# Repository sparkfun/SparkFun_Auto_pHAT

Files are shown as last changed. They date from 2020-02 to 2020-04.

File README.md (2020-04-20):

SparkFun Auto pHAT for Raspberry Pi (Qwiic)
========================================

SparkFun Auto pHAT for Raspberry Pi (Qwiic)) (https://www.sparkfun.com/products/16328)

[*SparkFun Auto pHAT for Raspberry Pi (Qwiic) (ROB-16328)*](https://www.sparkfun.com/products/16328)

The SparkFun Auto pHAT for Raspberry Pi is an all in one robotics package that focuses on quickly adding robot functionality and support to your Raspberry Pi or other single-board computer. The Auto pHAT can drive two small DC motors with or without encoders and up to four servo motors in a straightforward manner via an I<sup>2</sup>C connection. The servo control is based on the [SparkFun servo pHAT](https://www.sparkfun.com/products/15316) and thanks to its I<sup>2</sup>C capabilities, this PWM add-on saves the Raspberry Pi's GPIO pins, allowing you to use them for other purposes. We have also provided a Qwiic connector for easy interfacing with the I<sup>2</sup>C bus using the [Qwiic system](https://www.sparkfun.com/qwiic). Whether you use the Auto pHAT with a Raspberry Pi, NVIDIA, Jetson Nano, Google Coral, or other SBC, it makes for a unique robotics addition for and board with a 2x20 GPIO.

The DC motor control comes from the same 4245 PSOC and 2-channel motor ports system used on the [SparkFun Qwiic Motor Driver](https://www.sparkfun.com/products/15451). This provides 1.2A steady state drive per channel (1.5A peak) and 127 levels of DC drive strength. The SparkFun Auto pHAT also supports up to two motor encoders thanks to the onboard ATTINY84A to provide more precise movement to your creation! 

Additionally, the Auto pHAT has an on-board ICM-20948 9DOF IMU for all your motion sensing needs. This enables your robot to access the 3-Axis Gyroscope with four selectable ranges, 3-Axis Accelerometer, again with four selectable ranges, and 3-axis magnetometer with an FSR of ±4900µT.

Power to the SparkFun Auto pHAT can be supplied through USB-C connector or external power. This will power either the motors only, or power the motors as well as the Raspberry Pi that is connected to the HAT. This USB-C connector can also be used to hook up the Pi via serial port connection to avoid having to use a monitor and keyboard for setting up the Pi. We've even added power protection circuits to the design, to avoid damage to power sources.

For reference on programming the ATTINY84:

FUSE BITS:
(Set fuses to run at 8MHz internal)
(Disable Brown Out Detect)

* LowFuse 0xE2 
* HighFuse 0xDF
* ExtendedFuse 0xFF

Repository Contents
-------------------

* **/Documentation** - Data sheets, additional product information
* **/Hardware** - Eagle design files (.brd, .sch)
* **/Hardware/Production** - Production panel files and gerbers (.brd)
* **/Firmware** - Firmware for the Dual Encoder Reader IC (ATTiny84) and the Motor Driver IC (4245 PSOC)

Documentation
--------------

* **[Hookup Guide](https://learn.sparkfun.com/tutorials/sparkfun-auto-phat-hookup-guide)** - Basic hookup guide for the SparkFun Auto pHAT for Raspberry Pi (Qwiic).

License Information
-------------------

This product is _**open source**_! 

Please review the LICENSE.md file for license information. 

If you have any questions or concerns on licensing, please contact technical support on our [SparkFun forums](https://forum.sparkfun.com/viewforum.php?f=152).

Distributed as-is; no warranty is given.

- Your friends at SparkFun.

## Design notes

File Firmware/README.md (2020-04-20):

SparkFun Auto pHAT for Raspberry Pi (Qwiic)
========================================

The SparkFun Auto pHAT for Raspberry Pi Has two separate pieces of firmware:

(1) The Motor Controller firmware on the 4245 PSOC on the Auto pHAT is identical to the firmware found on the [SparkFun Qwiic Motor Driver](https://www.sparkfun.com/products/15451).

[Serial Controller Motor Driver Firmware](https://github.com/sparkfun/Serial_Controlled_Motor_Driver)

(2) The Encoder Reader firmware on the ATTiny84 can be found at the following Github Repository:

[Qwiic Dual Encoder Reader Firmware](https://github.com/sparkfun/Qwiic_Dual_Encoder_Reader)

For reference on programming the ATTINY84:

FUSE BITS:
(Set fuses to run at 8MHz internal)
(Disable Brown Out Detect)

* LowFuse 0xE2 
* HighFuse 0xDF
* ExtendedFuse 0xFF

License Information
-------------------

This product is _**open source**_! 

Please review the LICENSE.md file for license information. 

If you have any questions or concerns on licensing, please contact technical support on our [SparkFun forums](https://forum.sparkfun.com/viewforum.php?f=152).

Distributed as-is; no warranty is given.

- Your friends at SparkFun.

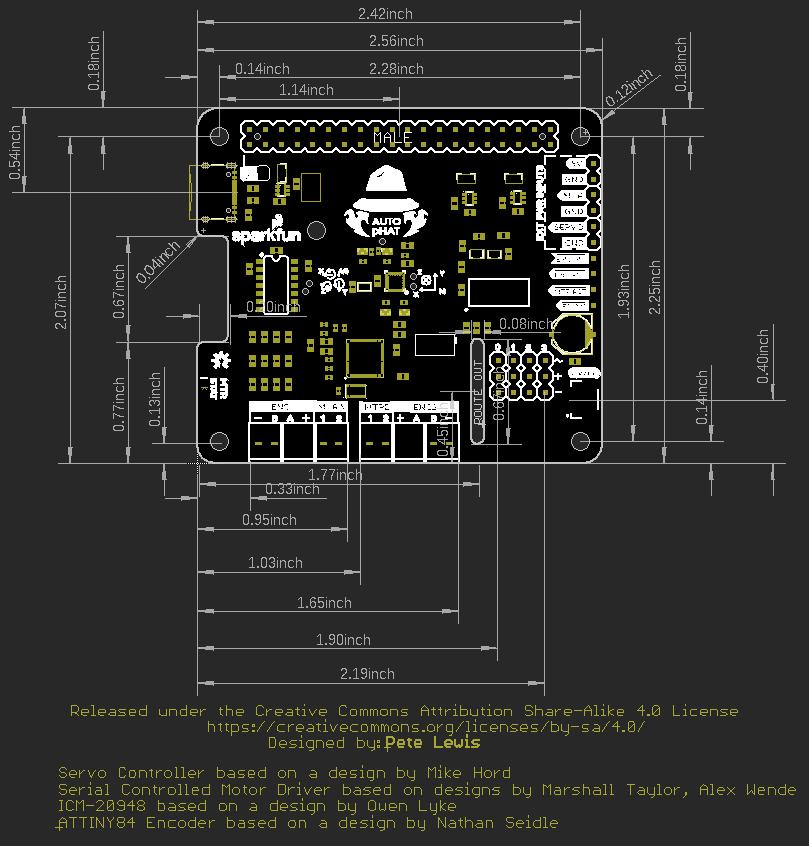
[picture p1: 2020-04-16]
Hardware/SparkFun_Auto_pHAT_Dimensions.png

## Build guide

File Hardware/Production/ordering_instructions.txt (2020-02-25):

panel size, 221x122mm
PCB thickness, 1.6mm
number of layers, 2
soldermask color, Red
silkscreen color, White
oz copper, 1oz
finish, HASL lead free
stencils, top+bottom
pcs per panel, 6
min trace width, 0.1778mm / 0.0070in
min drill size, 0.3500mm / 0.0138in

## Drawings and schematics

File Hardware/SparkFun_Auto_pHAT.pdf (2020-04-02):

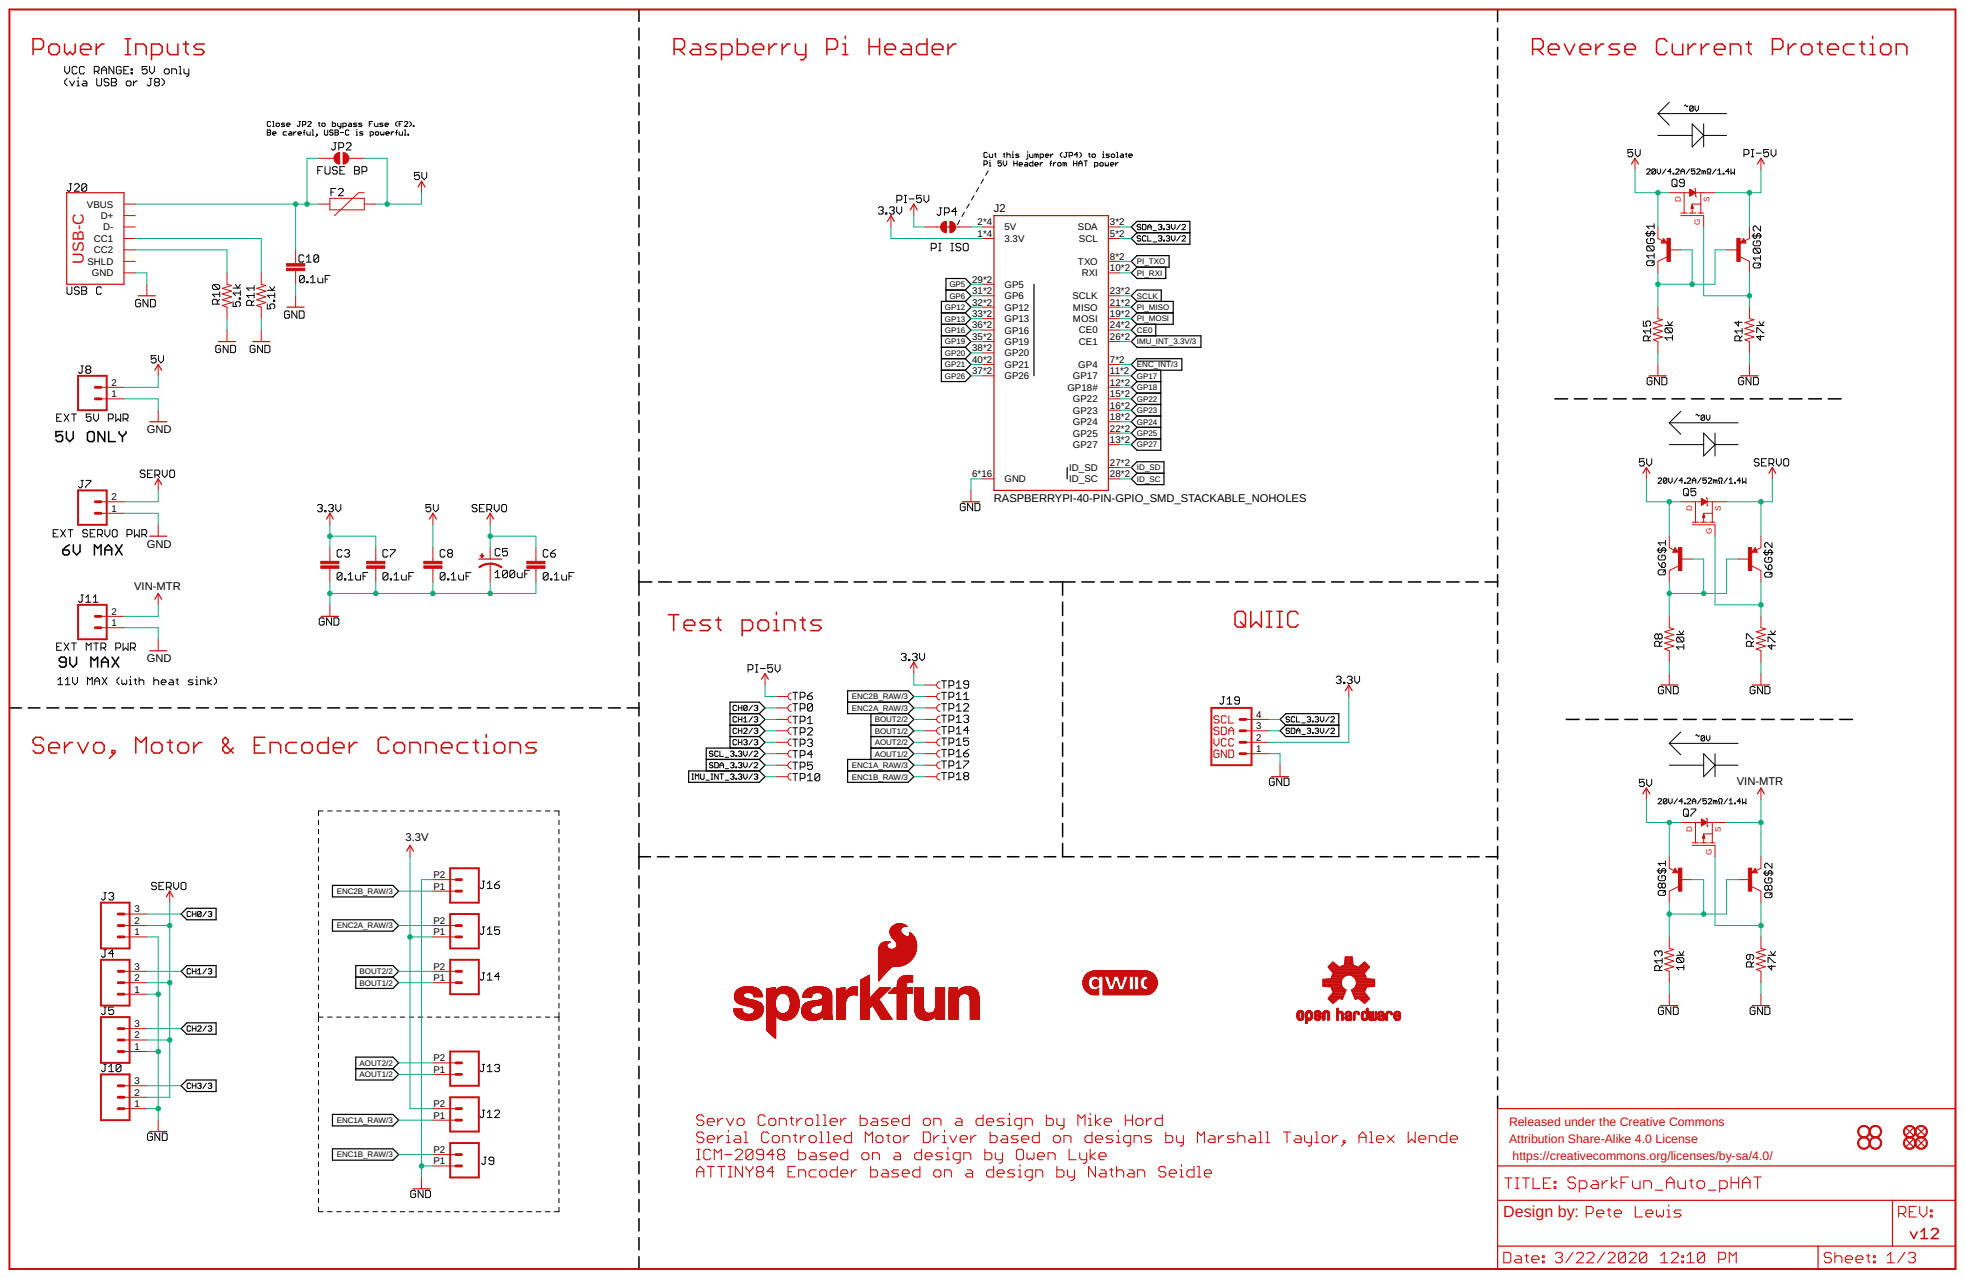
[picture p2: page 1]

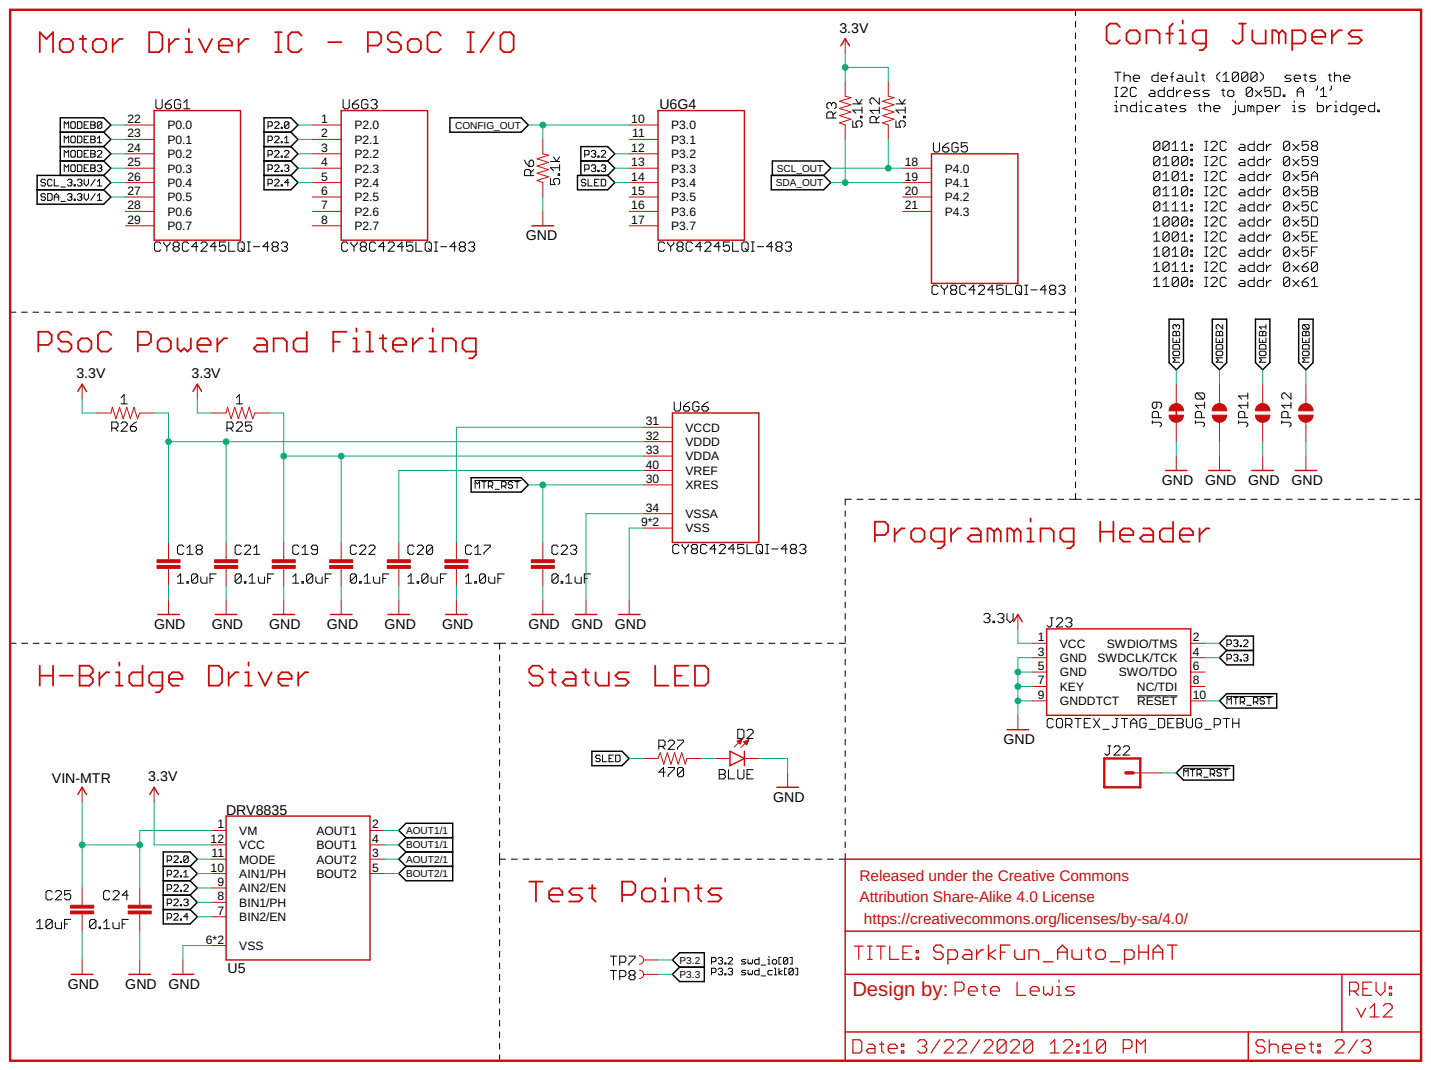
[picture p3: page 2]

GND GND

Released under the Creative Commons Attribution Share-Alike 4.0 License

https://creativecommons.org/licenses/by-sa/4.0/

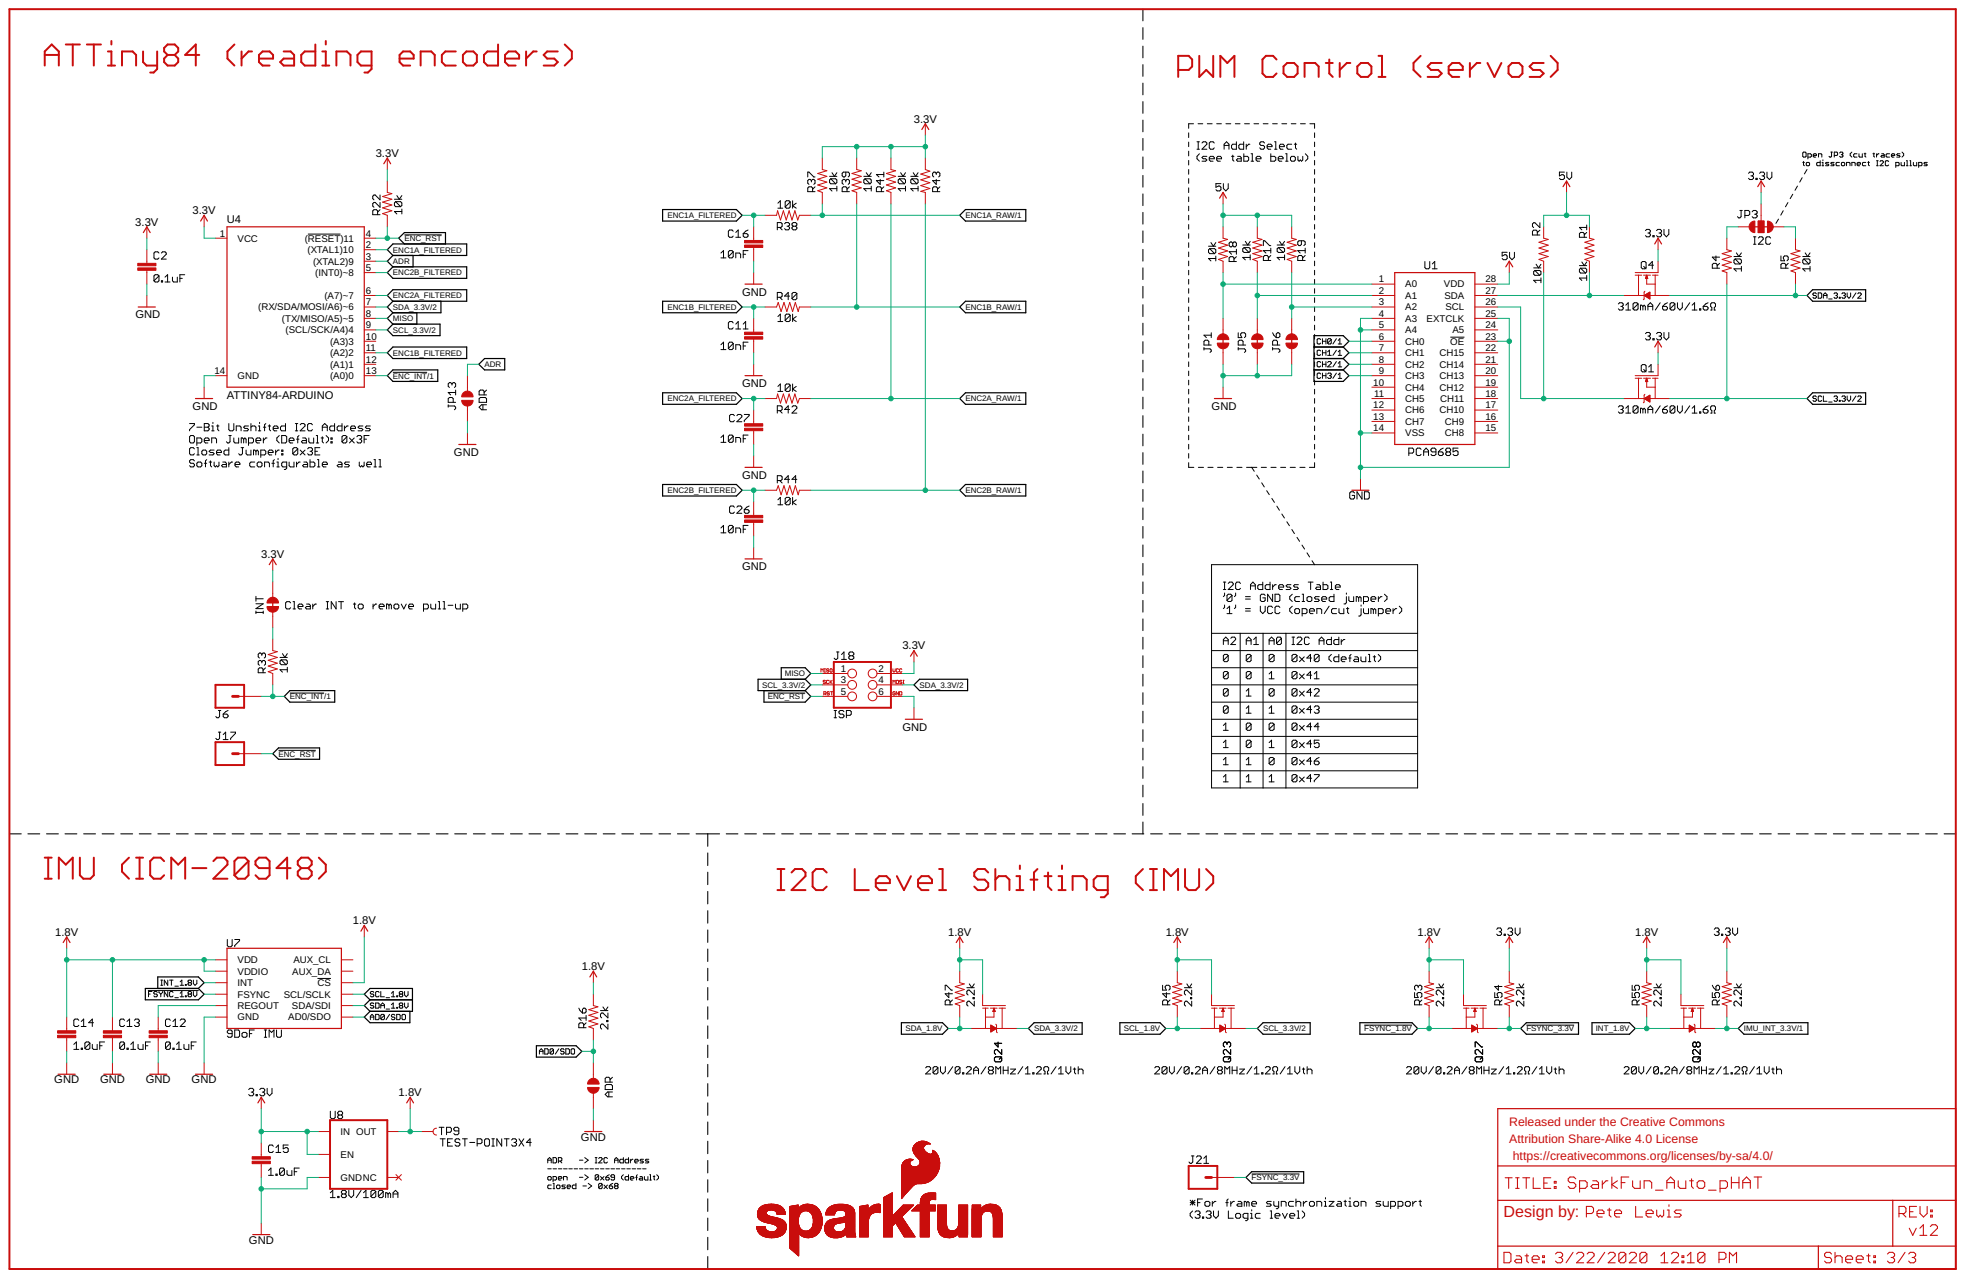
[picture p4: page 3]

SDA/SDI VDD
VDDIO
INT REGOUT SCL/SCLK
FSYNC GND

Released under the Creative Commons Attribution Share-Alike 4.0 License

https://creativecommons.org/licenses/by-sa/4.0/ Design by:

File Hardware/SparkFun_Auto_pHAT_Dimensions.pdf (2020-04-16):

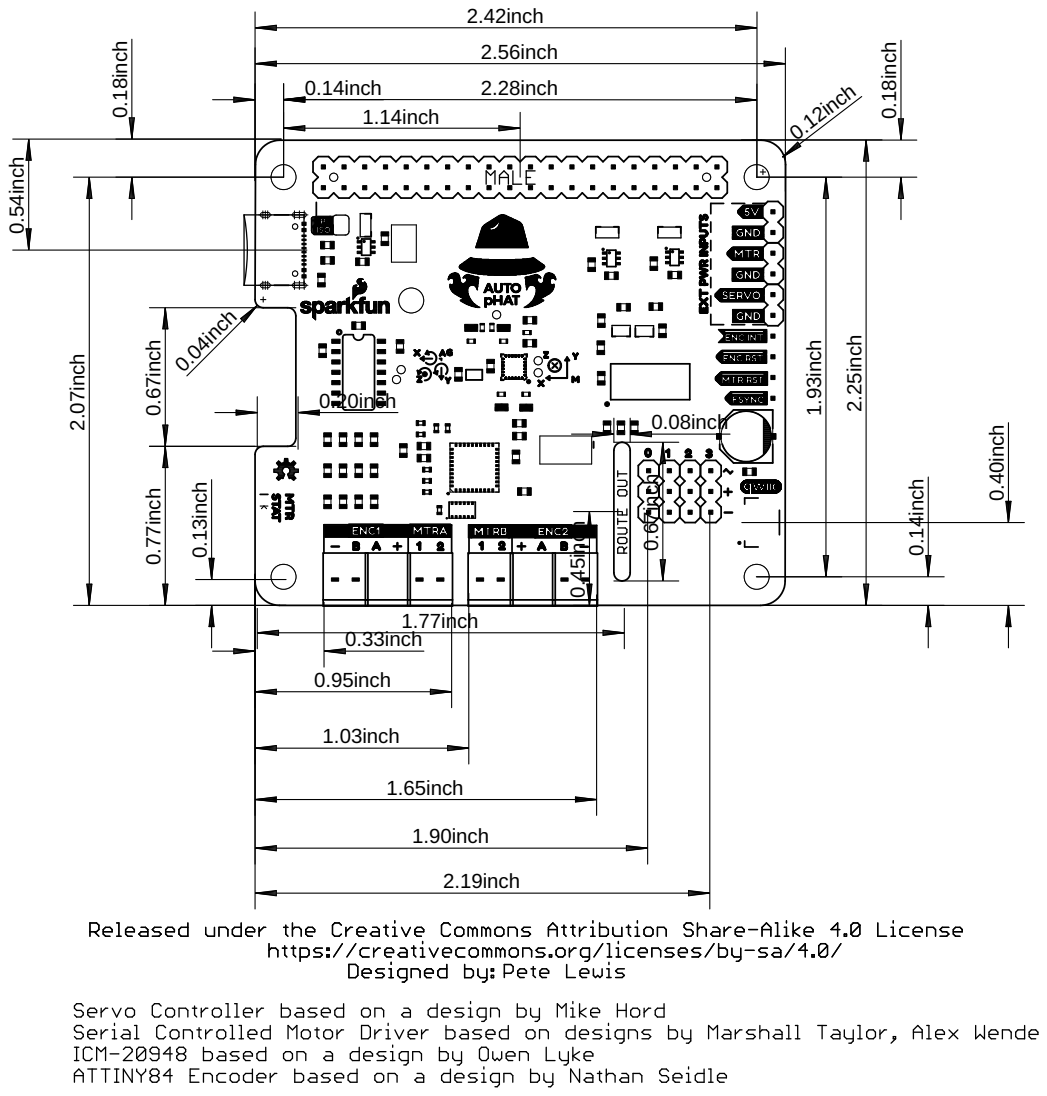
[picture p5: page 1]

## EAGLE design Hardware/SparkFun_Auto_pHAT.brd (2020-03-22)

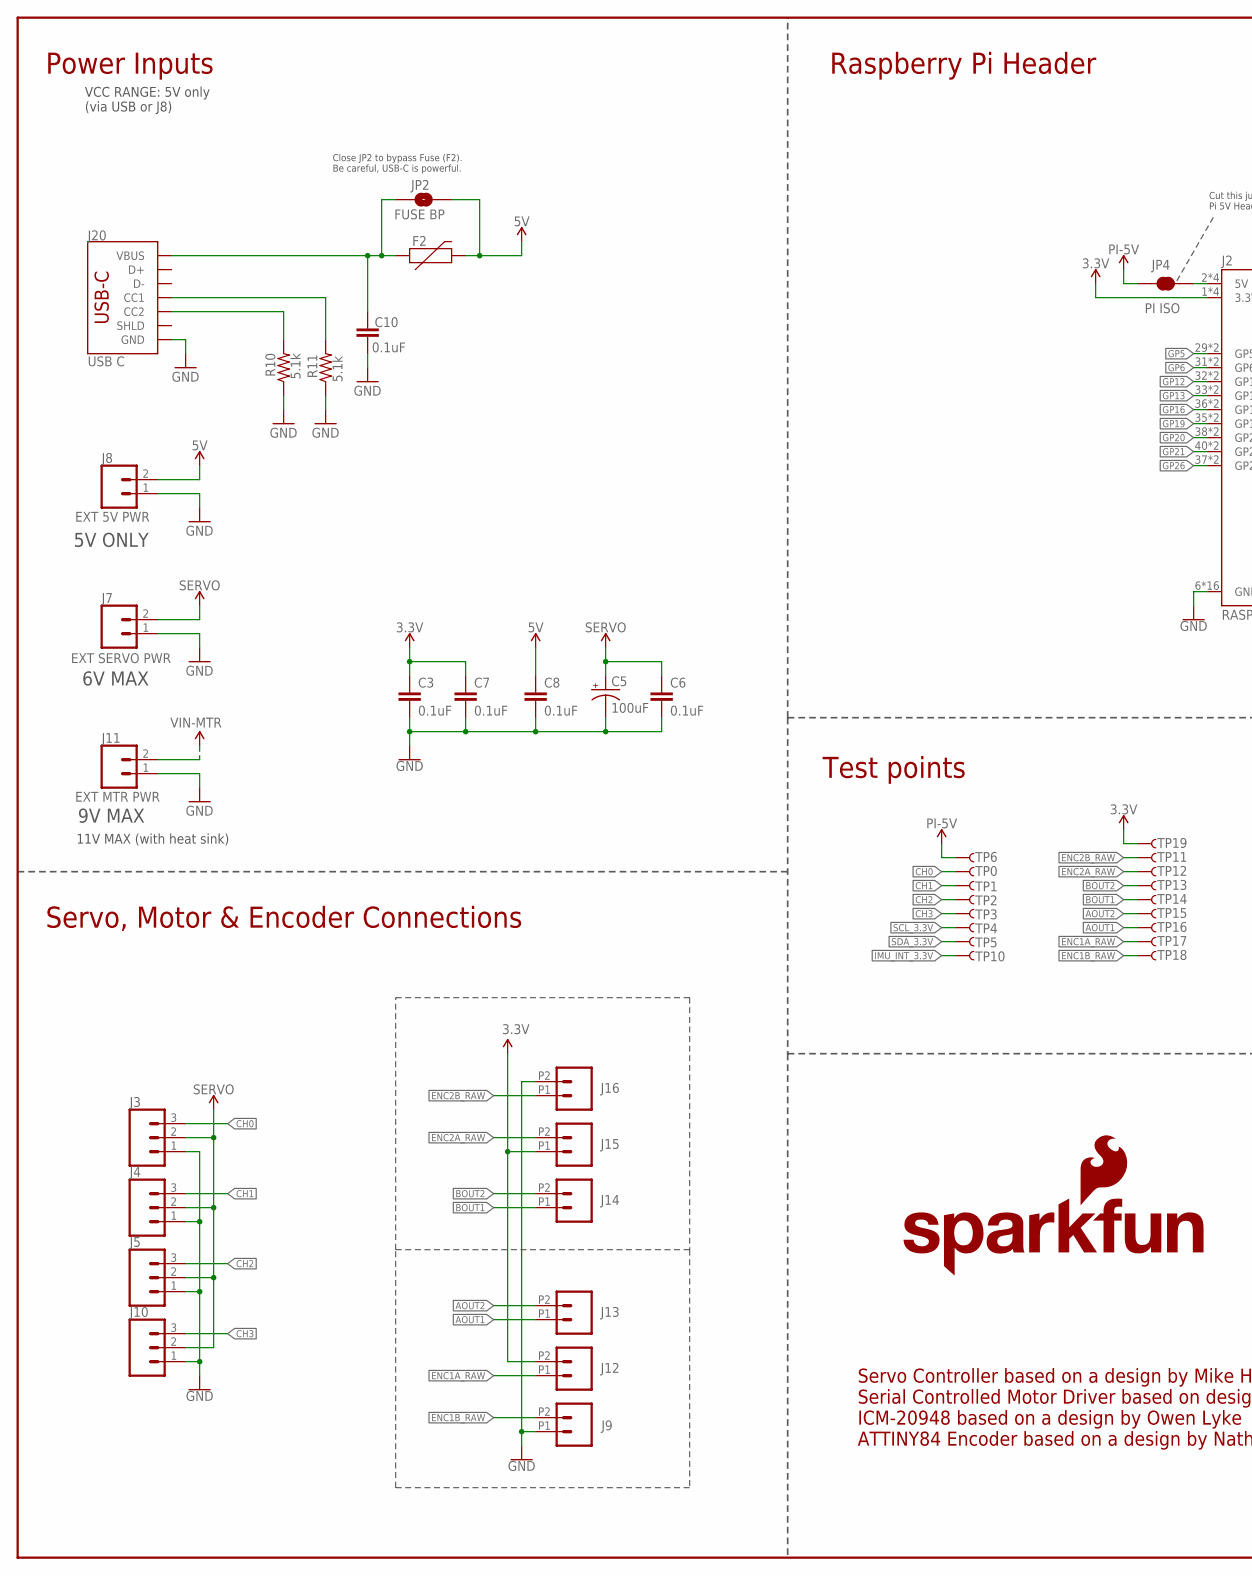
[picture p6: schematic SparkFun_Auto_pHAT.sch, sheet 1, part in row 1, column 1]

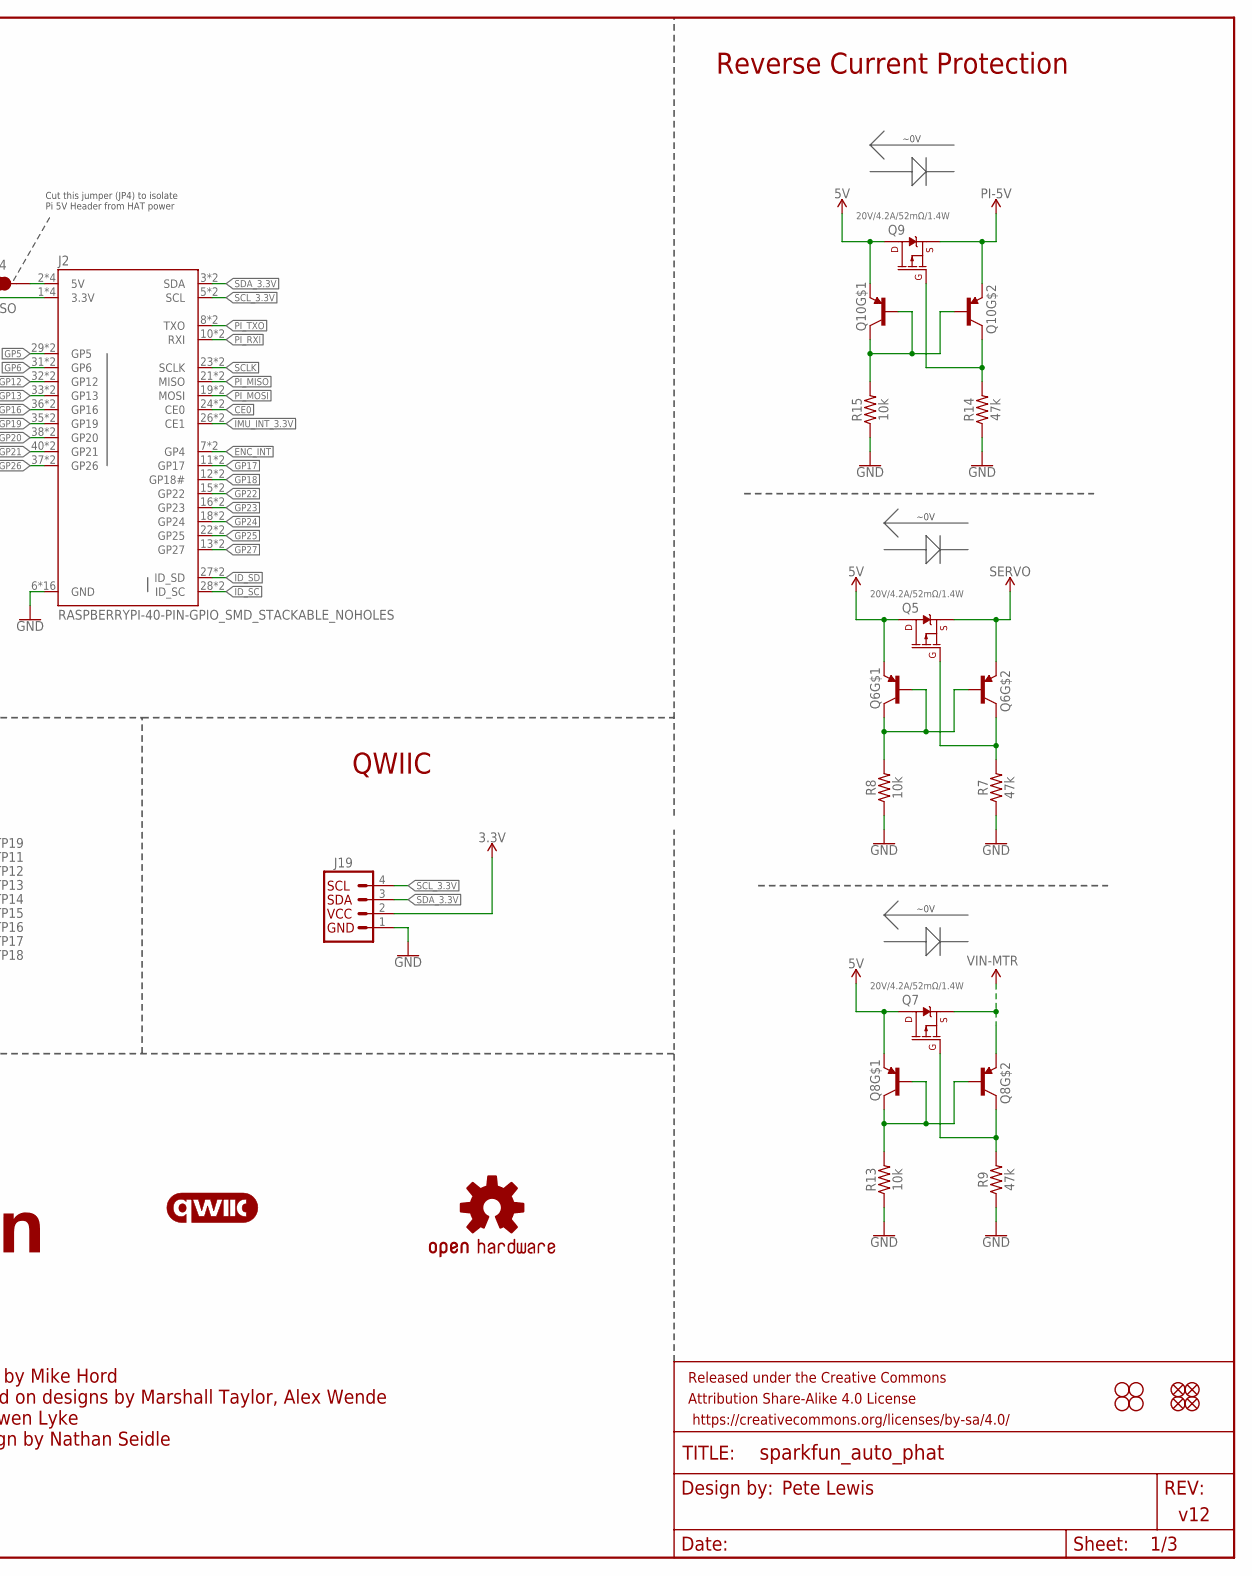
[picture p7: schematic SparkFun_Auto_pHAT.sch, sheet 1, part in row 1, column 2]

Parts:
C3, C6, C7, C8, C10: 0.1uF; 0603
C5: 100uF; PANASONIC_D
F2: 16V/2.5A(5A TRIP); 1812
FD5, FD6, FD7, FD8: FIDUCIALUFIDUCIAL; FIDUCIAL-MICRO
FRAME2: FRAME-LEDGER; CREATIVE_COMMONS
H9, H10, H11, H12: STAND-OFFTIGHT; STAND-OFF-TIGHT
J2: RASPBERRYPI-40-PIN-GPIO_SMD_STACKABLE_NOHOLES; RASPBERRY_PI_HAT_40_PIN_SMD_STACKABLE_NOHOLES
J3, J4, J5, J10: CONN_03LOCK; 1X03_LOCK
J7: EXT SERVO PWR; 1X02
J8: EXT 5V PWR; 1X02
J9, J13, J14, J16: CONN_02LG_DRILL; 1X02_2.54_SCREWTERM_LG_DRILL
J11: EXT MTR PWR; 1X02
J12, J15: CONN_022.54MM_SCREWTERM; 1X02_2.54_SCREWTERM
J19: QWIIC_CONNECTORJS-1MM; JST04_1MM_RA
J20: USB C; USB-C-16P
JP2: FUSE BP; SMT-JUMPER_2_NO_SILK
JP4: PI ISO; SMT-JUMPER_2_NC_TRACE_SILK
LOGO1: SFE_LOGO_NAME_FLAME.1_INCH; SFE_LOGO_NAME_FLAME_.1
LOGO2: OSHW-LOGOS; OSHW-LOGO-S
Q5, Q7, Q9: 20V/4.2A/52mΩ/1.4W; SOT23-3
Q6, Q8, Q10: TRANS_PNP_DUALSOT-363; SOT363_PHILIPS
R7, R9, R14: 47k; 0603@1
R8, R13, R15: 10k; 0603@1
R10, R11: 5.1k; 0603@1
TP0, TP1, TP2, TP3, TP6, TP10, TP11, TP12, TP13, TP14, TP15, TP16, TP17, TP18: TEST-POINT3X4; PAD.03X.04
TP4, TP5, TP19: TEST-POINTTP_15TH_THRU; TP_15TH
U$1: QWIIC_LOGO_5MM; QWIIC_5MM

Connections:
3.3V: C3.1, C7.1, J2.1 (3.3V), J2.1B (3.3V), J2.17 (3.3V), J2.17B (3.3V), J12.P2 (2), J15.P1 (1), J19.2, TP19.P$1; also elsewhere on the board
5V: C8.1, F2.2, J8.2, JP2.2, Q5.3 (D), Q6.1 (E), Q7.3 (D), Q8.1 (E), Q9.3 (D), Q10.1 (E); also elsewhere on the board
!ENC_INT: J2.7 (GP4), J2.7B (GP4); also elsewhere on the board
AOUT1: J13.P1 (1), TP16.P$1; also elsewhere on the board
AOUT2: J13.P2 (2), TP15.P$1; also elsewhere on the board
BOUT1: J14.P1 (1), TP14.P$1; also elsewhere on the board
BOUT2: J14.P2 (2), TP13.P$1; also elsewhere on the board
CC1: J20.A5 (CC1), R11.2
CC2: J20.B5 (CC2), R10.2
CE0: J2.24 (CE0), J2.24B (CE0)
CH0: J3.3, TP0.P$1; also elsewhere on the board
CH1: J4.3, TP1.P$1; also elsewhere on the board
CH2: J5.3, TP2.P$1; also elsewhere on the board
CH3: J10.3, TP3.P$1; also elsewhere on the board
ENC1A_RAW: J12.P1 (1), TP17.P$1; also elsewhere on the board
ENC1B_RAW: J9.P2 (2), TP18.P$1; also elsewhere on the board
ENC2A_RAW: J15.P2 (2), TP12.P$1; also elsewhere on the board
ENC2B_RAW: J16.P1 (1), TP11.P$1; also elsewhere on the board
GND: C3.2, C5.-, C6.2, C7.2, C8.2, C10.2, J2.6 (GND), J2.6B (GND), J2.9 (GND), J2.9B (GND), J2.14 (GND), J2.14B (GND), J2.20 (GND), J2.20B (GND), J2.25 (GND), J2.25B (GND), J2.30 (GND), J2.30B (GND), J2.34 (GND), J2.34B (GND), J2.39 (GND), J2.39B (GND), J3.1, J4.1, J5.1, J7.1, J8.1, J9.P1 (1), J10.1, J11.1, J16.P2 (2), J19.1, J20.GND, J20.GND2 (GND), R7.1, R8.1, R9.1, R10.1, R11.1, R13.1, R14.1, R15.1; also elsewhere on the board
GP5: J2.29 (GP5), J2.29B (GP5)
GP6: J2.31 (GP6), J2.31B (GP6)
GP12: J2.32 (GP12), J2.32B (GP12)
GP13: J2.33 (GP13), J2.33B (GP13)
GP16: J2.36 (GP16), J2.36B (GP16)
GP17: J2.11 (GP17), J2.11B (GP17)
GP18: J2.12 (GP18#), J2.12B (GP18#)
GP19: J2.35 (GP19), J2.35B (GP19)
GP20: J2.38 (GP20), J2.38B (GP20)
GP21: J2.40 (GP21), J2.40B (GP21)
GP22: J2.15 (GP22), J2.15B (GP22)
GP23: J2.16 (GP23), J2.16B (GP23)
GP24: J2.18 (GP24), J2.18B (GP24)
GP25: J2.22 (GP25), J2.22B (GP25)
GP26: J2.37 (GP26), J2.37B (GP26)
GP27: J2.13 (GP27), J2.13B (GP27)
ID_SC: J2.28 (ID_SC), J2.28B (ID_SC)
ID_SD: J2.27 (ID_SD), J2.27B (ID_SD)
IMU_INT_3.3V: J2.26 (CE1), J2.26B (CE1), TP10.P$1; also elsewhere on the board
unnamed: Q5.1 (G), Q6.3 (C), R7.2
unnamed: Q6.2 (B), Q6.5 (B), Q6.6 (C), R8.2
unnamed: Q7.1 (G), Q8.3 (C), R9.2
unnamed: Q8.2 (B), Q8.5 (B), Q8.6 (C), R13.2
unnamed: Q9.1 (G), Q10.3 (C), R14.2
unnamed: Q10.2 (B), Q10.5 (B), Q10.6 (C), R15.2
unnamed: J2.2 (5V), J2.2B (5V), J2.4 (5V), J2.4B (5V), JP4.2
PI-5V: JP4.1, Q9.2 (S), Q10.4 (E), TP6.P$1
PI_MISO: J2.21 (MISO), J2.21B (MISO)
PI_MOSI: J2.19 (MOSI), J2.19B (MOSI)
PI_RXI: J2.10 (RXI), J2.10B (RXI)
PI_TXO: J2.8 (TXO), J2.8B (TXO)
SCLK: J2.23 (SCLK), J2.23B (SCLK)
SCL_3.3V: J2.5 (SCL), J2.5B (SCL), J19.4, TP4.P$1; also elsewhere on the board
SDA_3.3V: J2.3 (SDA), J2.3B (SDA), J19.3, TP5.P$1; also elsewhere on the board
SERVO: C5.+, C6.1, J3.2, J4.2, J5.2, J7.2, J10.2, Q5.2 (S), Q6.4 (E)
VBUS: C10.1, F2.1, J20.VBUS1 (VBUS), J20.VBUS2 (VBUS), JP2.1
VIN-MTR: J11.2, Q7.2 (S), Q8.4 (E); also elsewhere on the board

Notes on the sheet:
Pete Lewis
v12
Raspberry Pi Header
Servo, Motor & Encoder Connections
Cut this jumper (JP4) to isolate Pi 5V Header from HAT power
Power Inputs
Close JP2 to bypass Fuse (F2). Be careful, USB-C is powerful.
VCC RANGE: 5V only (via USB or J8)
~0V
QWIIC
Reverse Current Protection
Test points
9V MAX
6V MAX
5V ONLY
Servo Controller based on a design by Mike Hord Serial Controlled Motor Driver based on designs by Marshall Taylor, Alex Wende ICM-20948 based on a design by Owen Lyke ATTINY84 Encoder based on a design by Nathan Seidle
11V MAX (with heat sink)

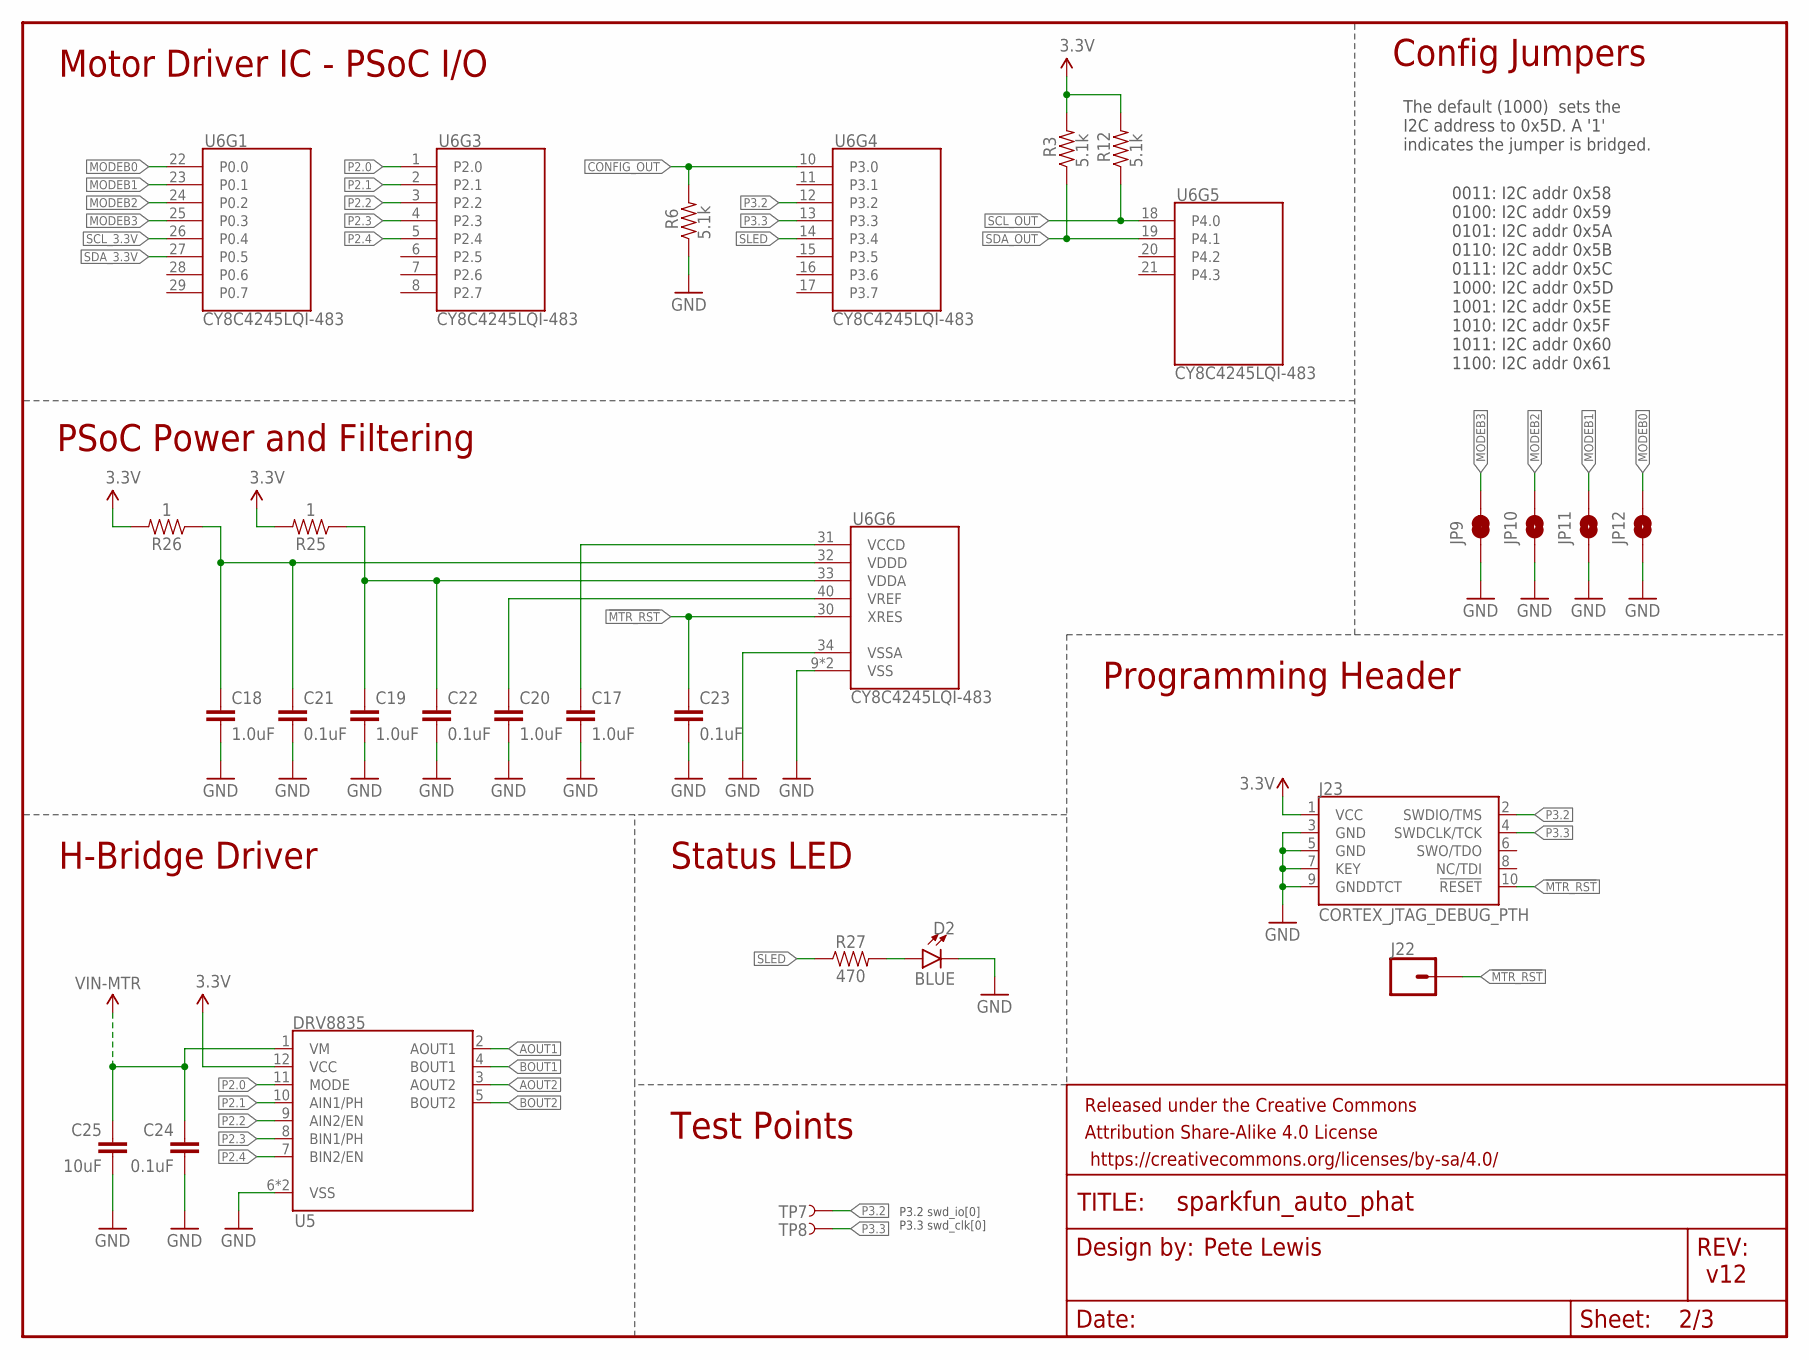
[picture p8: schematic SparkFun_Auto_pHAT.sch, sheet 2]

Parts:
C17, C18, C19, C20: 1.0uF; 0402
C21, C22, C23, C24: 0.1uF; 0402
C25: 10uF; 0805
D2: BLUE; LED-0603@1
FRAME1: FRAME-LETTERNO_PACKAGE; DUMMY
J22: CONN_01PTH_NO_SILK_YES_STOP; 1X01_NO_SILK
J23: CORTEX_JTAG_DEBUG_PTH; 2X5-PTH-1.27MM
JP9: JUMPER-PAD-2; SMT-JUMPER_2_NC_TRACE_NO-SILK
JP10, JP11, JP12: JUMPER-PAD-2; SMT-JUMPER_2_NO_NO-SILK
R3, R6, R12: 5.1k; 0603@1
R25, R26: 1; 0603@1
R27: 470; 0603@1
TP7, TP8: TEST-POINT3X4; PAD.03X.04
U5: DRV8835; WSON-12
U6: CY8C4245LQI-483; QFN-40

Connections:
3.3V: J23.1 (VCC), R3.2, R12.2, R25.2, R26.2, U5.12 (VCC); also elsewhere on the board
!MTR_RST: C23.1, J22.1, J23.10 (!RESET), U6.30 (XRES)
AOUT1: U5.2 (AOUT1); also elsewhere on the board
AOUT2: U5.3 (AOUT2); also elsewhere on the board
BOUT1: U5.4 (BOUT1); also elsewhere on the board
BOUT2: U5.5 (BOUT2); also elsewhere on the board
CONFIG_OUT: R6.2, U6.10 (P3.0)
GND: C17.2, C18.2, C19.2, C20.2, C21.2, C22.2, C23.2, C24.2, C25.2, D2.C, J23.3 (GND), J23.5 (GND), J23.7 (KEY), J23.9 (GNDDTCT), JP9.1, JP10.1, JP11.1, JP12.1, R6.1, U5.6 (VSS), U5.PAD (VSS), U6.9 (VSS), U6.34 (VSSA), U6.EP (VSS); also elsewhere on the board
MODEB0: JP12.2, U6.22 (P0.0)
MODEB1: JP11.2, U6.23 (P0.1)
MODEB2: JP10.2, U6.24 (P0.2)
MODEB3: JP9.2, U6.25 (P0.3)
unnamed: C17.1, U6.31 (VCCD)
unnamed: C19.1, C22.1, R25.1, U6.33 (VDDA)
unnamed: C20.1, U6.40 (VREF)
unnamed: D2.A, R27.2
P2.0: U5.11 (MODE), U6.1 (P2.0)
P2.1: U5.10 (AIN1/PH), U6.2 (P2.1)
P2.2: U5.9 (AIN2/EN), U6.3 (P2.2)
P2.3: U5.8 (BIN1/PH), U6.4 (P2.3)
P2.4: U5.7 (BIN2/EN), U6.5 (P2.4)
P3.2: J23.2 (SWDIO/TMS), TP7.P$1, U6.12 (P3.2)
P3.3: J23.4 (SWDCLK/TCK), TP8.P$1, U6.13 (P3.3)
SCL_3.3V: U6.26 (P0.4); also elsewhere on the board
SCL_OUT: R12.1, U6.18 (P4.0)
SDA_3.3V: U6.27 (P0.5); also elsewhere on the board
SDA_OUT: R3.1, U6.19 (P4.1)
SLED: R27.1, U6.14 (P3.4)
VDDD1: C18.1, C21.1, R26.1, U6.32 (VDDD)
VIN-MTR: C24.1, C25.1, U5.1 (VM); also elsewhere on the board

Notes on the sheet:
PSoC Power and Filtering
Config Jumpers
Pete Lewis
Motor Driver IC - PSoC I/O
v12
P3.2 swd_io[0] P3.3 swd_clk[0]
0011: I2C addr 0x58 0100: I2C addr 0x59 0101: I2C addr 0x5A 0110: I2C addr 0x5B 0111: I2C addr 0x5C 1000: I2C addr 0x5D 1001: I2C addr 0x5E 1010: I2C addr 0x5F 1011: I2C addr 0x60 1100: I2C addr 0x61
The default (1000) sets the I2C address to 0x5D. A '1' indicates the jumper is bridged.
Status LED
H-Bridge Driver
Test Points
Programming Header

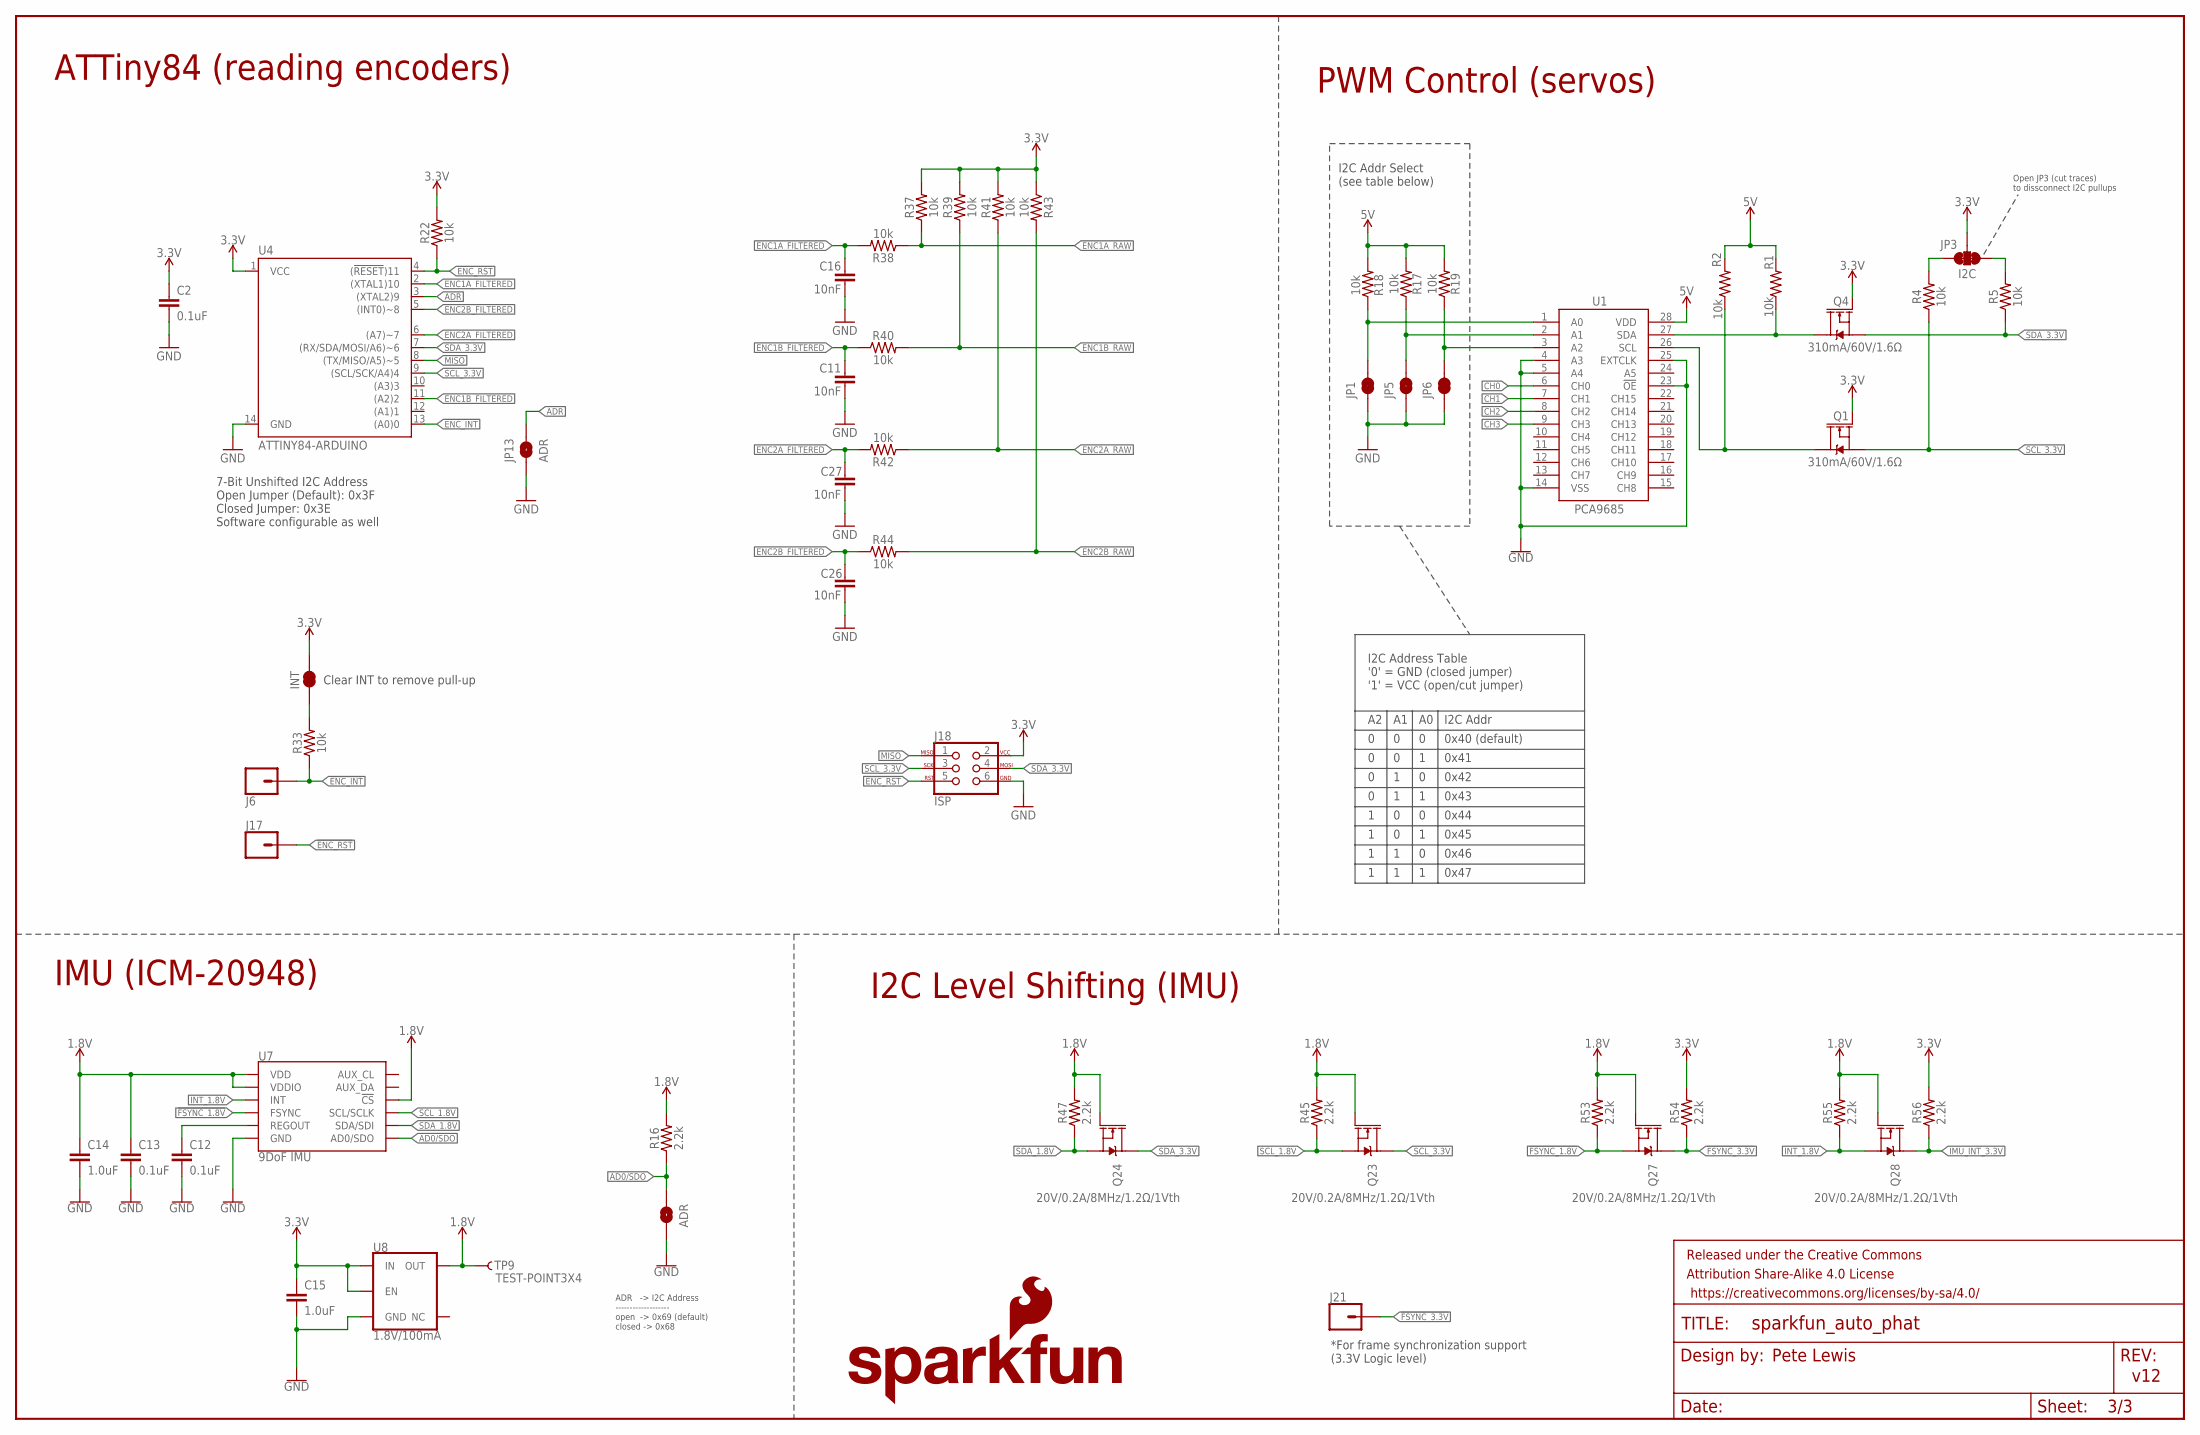
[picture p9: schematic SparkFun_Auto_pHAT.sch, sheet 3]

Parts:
C2, C12, C13: 0.1uF; 0603
C11, C16, C26, C27: 10nF; 0603
C14, C15: 1.0uF; 0603
FRAME3: FRAME-LEDGER; CREATIVE_COMMONS
INT: JUMPER-SMT_2_NC_TRACE_SILK; SMT-JUMPER_2_NC_TRACE_SILK
J6, J17, J21: CONN_01PTH_NO_SILK_YES_STOP; 1X01_NO_SILK
J18: ISP; 2X3_TEST_POINTS
JP1, JP5, JP6: JUMPER-PAD-2; SMT-JUMPER_2_NC_TRACE_NO-SILK
JP3: I2C; SMT-JUMPER_3_2-NC_TRACE_SILK
JP13, JP15: ADR; SMT-JUMPER_2_NO_SILK
LOGO4: SFE_LOGO_NAME_FLAME.1_INCH; SFE_LOGO_NAME_FLAME_.1
Q1, Q4: 310mA/60V/1.6Ω; SOT323
Q23, Q24, Q27, Q28: 20V/0.2A/8MHz/1.2Ω/1Vth; SOT-416FL
R1, R2, R4, R5, R17, R18, R19, R22, R33, R37, R38, R39, R40, R41, R42, R43, R44: 10k; 0603@1
R16, R45, R47, R53, R54, R55, R56: 2.2k; 0402-TIGHT
TP9: TEST-POINT3X4; PAD.03X.04
U1: PCA9685; TSSOP-28_4MM
U4: ATTINY84-ARDUINO; SO14
U7: 9DoF IMU; QFN24-3X3
U8: 1.8V/100mA; SC70

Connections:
1.8V: C13.1, C14.1, Q23.1 (G), Q24.1 (G), Q27.1 (G), Q28.1 (G), R16.2, R45.2, R47.2, R53.2, R55.2, TP9.P$1, U7.8 (VDDIO), U7.13 (VDD), U7.22 (!CS), U8.5 (OUT)
3.3V: C2.1, C15.1, INT.2, J18.2, JP3.2, Q1.1 (G), Q4.1 (G), R22.2, R37.2, R39.2, R41.2, R43.1, R54.2, R56.2, U4.1 (VCC), U8.1 (IN), U8.3 (EN); also elsewhere on the board
5V: R1.2, R2.2, R17.2, R18.2, R19.2, U1.28 (VDD); also elsewhere on the board
!ENC_INT: J6.1, R33.1, U4.13 ((A0)0); also elsewhere on the board
!ENC_RST: J17.1, J18.5, R22.1, U4.4 ((!RESET!)11)
!FSYNC_1.8V: Q27.2 (S), R53.1, U7.11 (FSYNC)
!FSYNC_3.3V: J21.1, Q27.3 (D), R54.1
AD0/SDO: JP15.2, R16.1, U7.9 (AD0/SDO)
ADD_A0: JP1.2, R18.1, U1.1 (A0)
ADD_A1: JP5.2, R17.1, U1.2 (A1)
ADD_A2: JP6.2, R19.1, U1.3 (A2)
ADR: JP13.2, U4.3 ((XTAL2)9)
CH0: U1.6 (CH0); also elsewhere on the board
CH1: U1.7 (CH1); also elsewhere on the board
CH2: U1.8 (CH2); also elsewhere on the board
CH3: U1.9 (CH3); also elsewhere on the board
ENC1A_FILTERED: C16.1, R38.2, U4.2 ((XTAL1)10)
ENC1A_RAW: R37.1, R38.1; also elsewhere on the board
ENC1B_FILTERED: C11.1, R40.1, U4.11 ((A2)2)
ENC1B_RAW: R39.1, R40.2; also elsewhere on the board
ENC2A_FILTERED: C27.1, R42.2, U4.6 ((A7)~7)
ENC2A_RAW: R41.1, R42.1; also elsewhere on the board
ENC2B_FILTERED: C26.1, R44.1, U4.5 ((INT0)~8)
ENC2B_RAW: R43.2, R44.2; also elsewhere on the board
GND: C2.2, C11.2, C12.2, C13.2, C14.2, C15.2, C16.2, C26.2, C27.2, J18.6, JP1.1, JP5.1, JP6.1, JP13.1, JP15.1, U1.4 (A3), U1.5 (A4), U1.14 (VSS), U1.23 (!OE), U1.25 (EXTCLK), U4.14 (GND), U7.18 (GND), U7.20 (GND), U8.2 (GND); also elsewhere on the board
IMU_INT_3.3V: Q28.3 (D), R56.1; also elsewhere on the board
INT_1.8V: Q28.2 (S), R55.1, U7.12 (INT)
INT_R: INT.1, R33.2
MISO: J18.1, U4.8 ((TX/MISO/A5)~5)
unnamed: JP3.3, R4.2
unnamed: Q1.3 (D), R2.1, U1.26 (SCL)
unnamed: Q4.3 (D), R1.1, U1.27 (SDA)
unnamed: JP3.1, R5.2
unnamed: C12.1, U7.10 (REGOUT)
SCL_1.8V: Q23.2 (S), R45.1, U7.23 (SCL/SCLK)
SCL_3.3V: J18.3, Q1.2 (S), Q23.3 (D), R4.1, U4.9 ((SCL/SCK/A4)4); also elsewhere on the board
SDA_1.8V: Q24.2 (S), R47.1, U7.24 (SDA/SDI)
SDA_3.3V: J18.4, Q4.2 (S), Q24.3 (D), R5.1, U4.7 ((RX/SDA/MOSI/A6)~6); also elsewhere on the board

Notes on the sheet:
IMU (ICM-20948)
I2C Level Shifting (IMU)
ADR -> I2C Address ------------------- open -> 0x69 (default) closed -> 0x68
7-Bit Unshifted I2C Address Open Jumper (Default): 0x3F Closed Jumper: 0x3E Software configurable as well
Clear INT to remove pull-up
ATTiny84 (reading encoders)
I2C Addr
Open JP3 (cut traces) to dissconnect I2C pullups
PWM Control (servos)
*For frame synchronization support (3.3V Logic level)
v12
Pete Lewis
I2C Addr Select (see table below)
0x40 (default)
0x41
0x42
0x43
0x44
0x45
0x46
0x47
I2C Address Table '0' = GND (closed jumper) '1' = VCC (open/cut jumper)

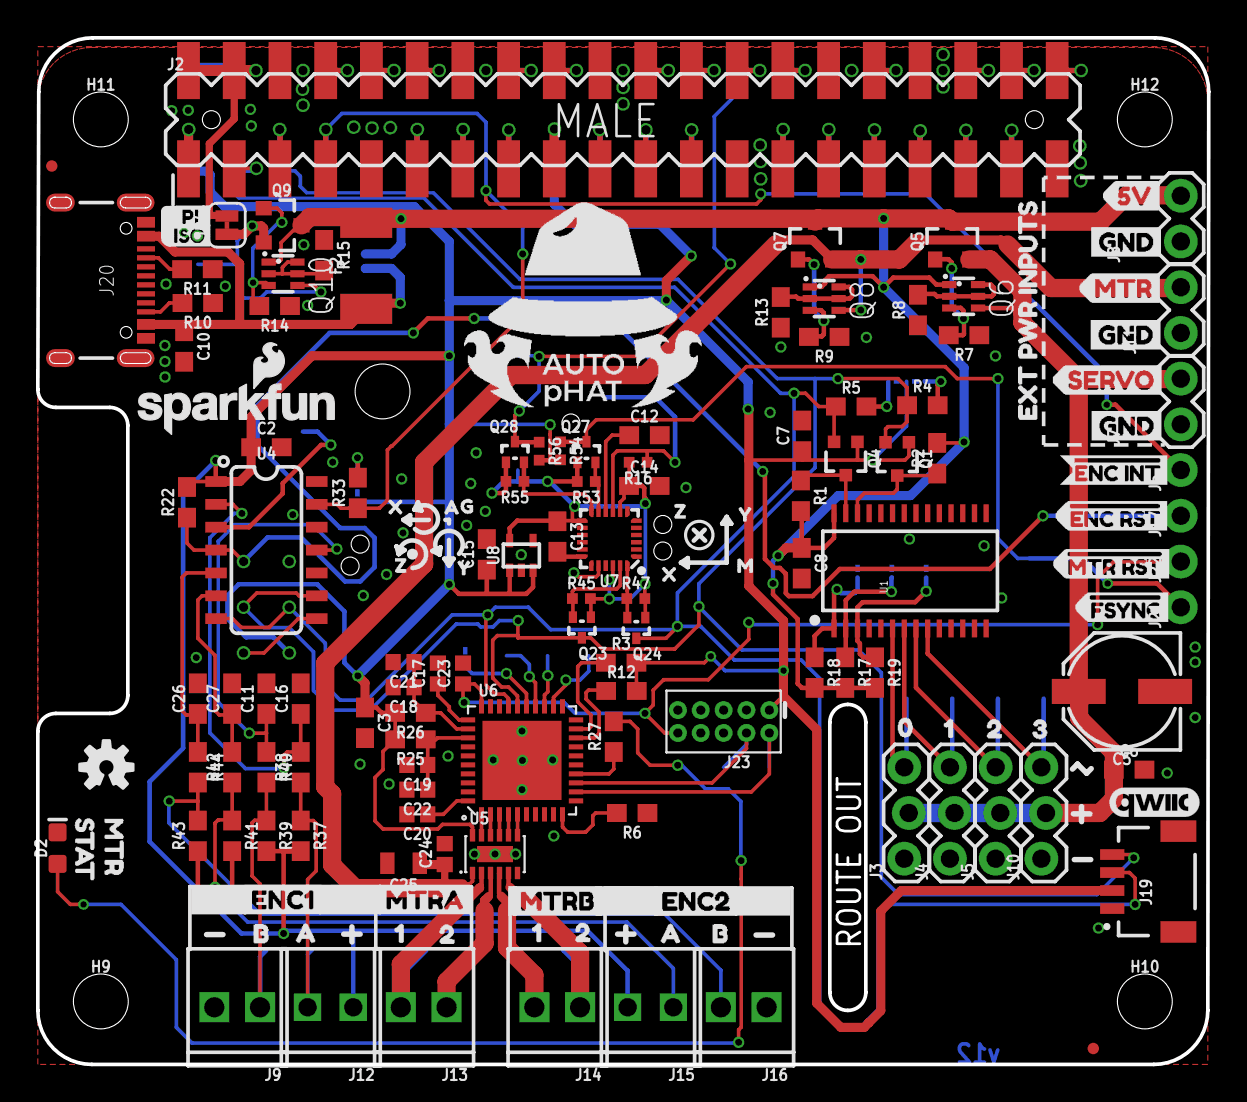
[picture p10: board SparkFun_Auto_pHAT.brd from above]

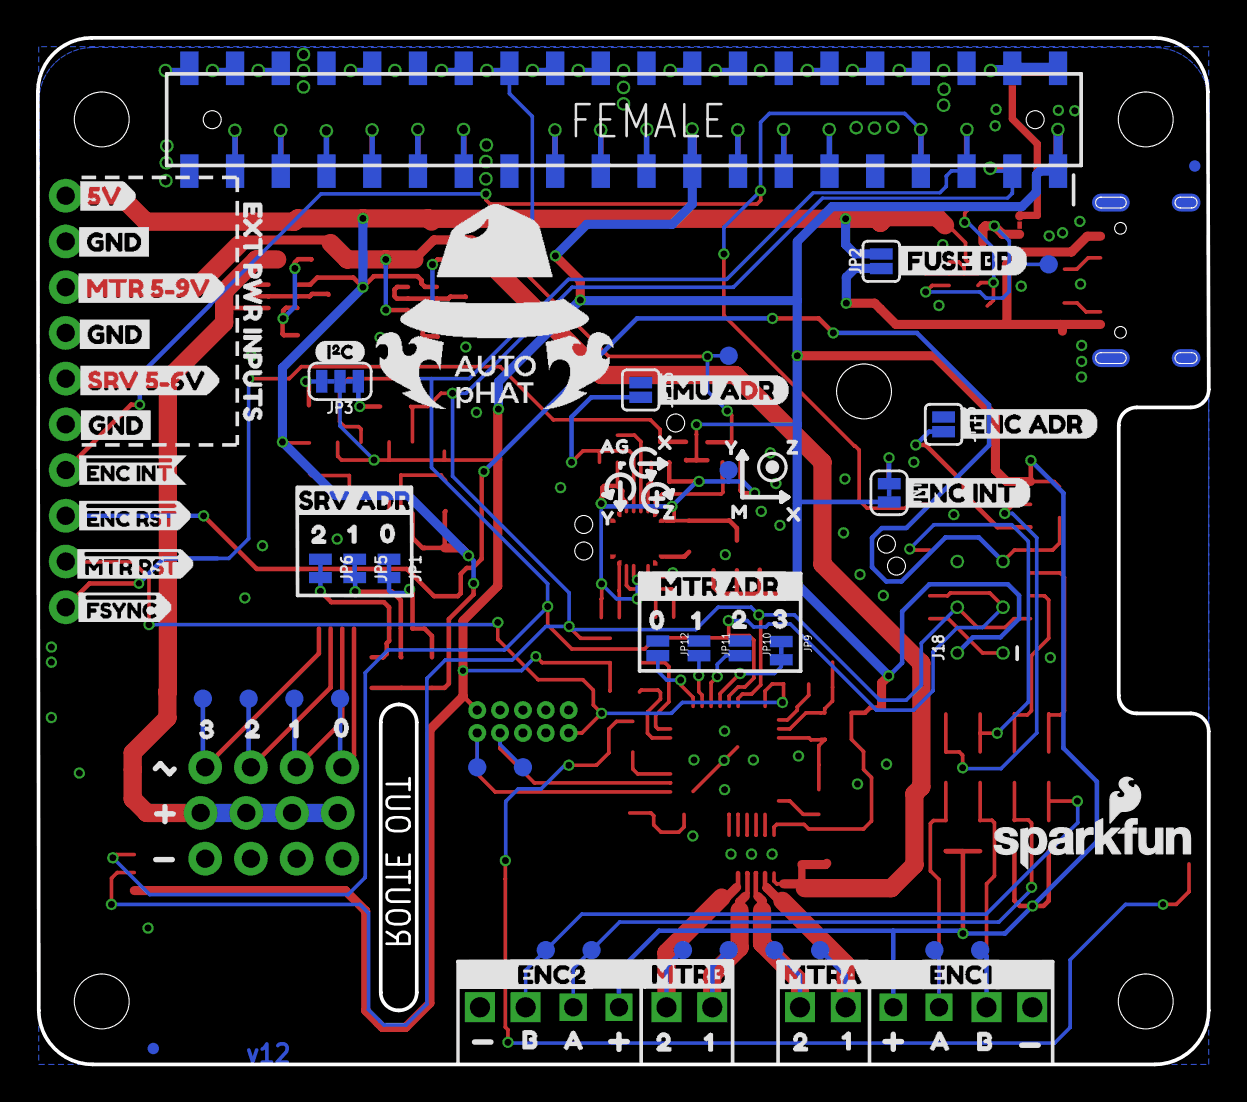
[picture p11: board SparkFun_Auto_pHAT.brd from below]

Board: 2 copper layers, 65.1 x 57.0 mm, 246 parts (84 on the bottom side), 100 nets.

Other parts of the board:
U$2: I_SUPER2_C-()-03
U$3, U$4, U$5, U$59, U$60, U$61: GND3
U$6, U$7, U$75, U$76: 10
U$8, U$79: 00
U$9: #MTR_RST5
U$10: #FSYNC7
U$11: #ENC_RST4
U$12: #ENC_INT6
U$13, U$52: EXT_PWR_INPUTS3
U$14: 5V2
U$15: MTR1
U$16: SERVO0
U$17, U$82: 11
U$18, U$19: 1X06_2.54_SCREWTERM_PIN_REF
U$20, U$21, U$65, U$66: B15
U$22, U$67: ENC112
U$23, U$68: ENC213
U$24, U$80: 22
U$25, U$81: 33
U$26, U$27, U$69, U$70: A14
U$29: STAT4
U$30: SRV_5#6V1
U$31, U$73: MTRA0
U$32: ISO1
U$33, U$41: 05
U$34, U$42: 16
U$35: PI0
U$36, U$45: 27
U$37: 38
U$38: MTR_5#9V0
U$39: IMU_ADR9
U$40, U$74: MTRB1
U$43, U$44, U$77, U$78: 21
U$46: MTR0
U$47: SRV_ADR0
U$48: ENC_INT12
U$49: ENC_ADR11
U$50: FUSE_BP10
U$51: MTR_ADR0
U$53: 5V3
U$56: #ENC_RST6
U$57: #MTR_RST7
U$58: #FSYNC8
U$62: #ENC_INT0
U$83, U$85: AUTOHAT-LOGO
U$103, U$109, U$123, U$126: X0
U$104, U$110, U$124, U$127: Y1
U$105, U$111, U$125, U$128: Z2
U$106, U$129: G5
U$107, U$130: A4
U$108, U$122: M3

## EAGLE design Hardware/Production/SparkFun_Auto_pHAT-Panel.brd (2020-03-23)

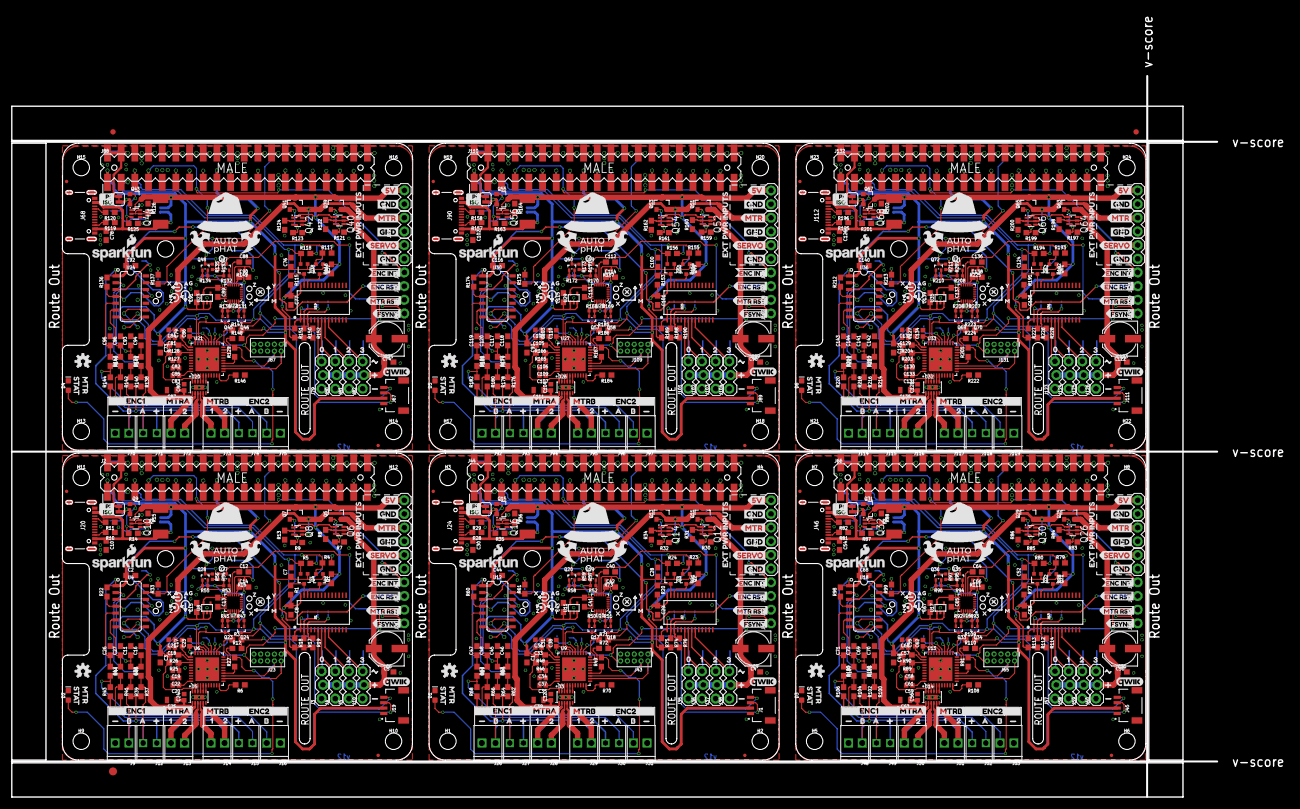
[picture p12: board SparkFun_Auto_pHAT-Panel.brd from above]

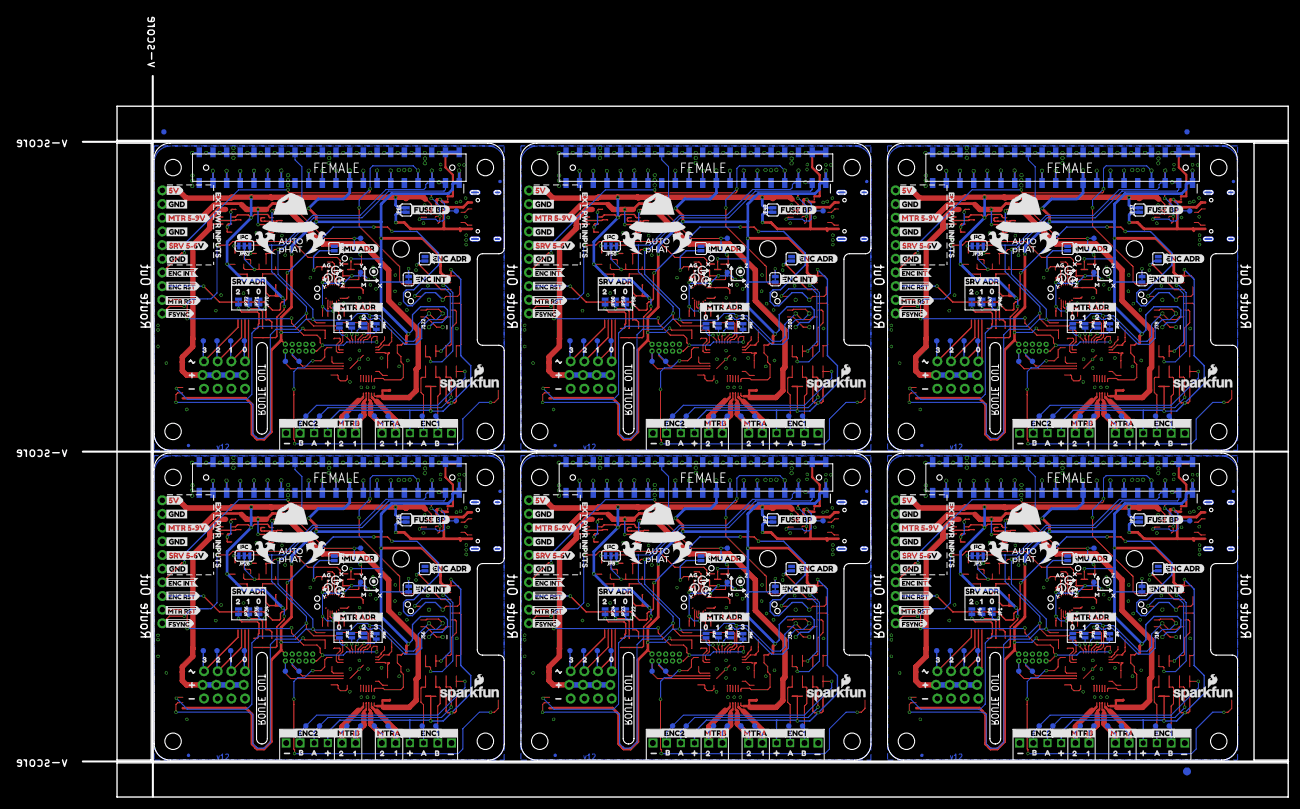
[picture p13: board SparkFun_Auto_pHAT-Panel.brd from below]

Board: 2 copper layers, 223.9 x 133.9 mm, 1482 parts (507 on the bottom side), 600 nets.

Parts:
C1, C2, C3, C6, C7, C8, C9, C10, C12, C13, C28, C29, C30, C40, C41, C44, C49, C51, C52, C53, C54, C64, C65, C68, C73, C75, C76, C77, C78, C88, C89, C92, C97, C99, C100, C101, C102, C112, C113, C116, C121, C123, C124, C125, C126, C136, C137, C140: 0.1uF; 0603
C4, C5, C50, C74, C98, C122: 100uF; PANASONIC_D
C11, C16, C26, C27, C45, C46, C47, C48, C69, C70, C71, C72, C93, C94, C95, C96, C117, C118, C119, C120, C141, C142, C143, C144: 10nF; 0603
C14, C15, C42, C43, C66, C67, C90, C91, C114, C115, C138, C139: 1.0uF; 0603
C17, C18, C19, C20, C31, C33, C34, C35, C55, C57, C58, C59, C79, C81, C82, C83, C103, C105, C106, C107, C127, C129, C130, C131: 1.0uF; 0402
C21, C22, C23, C24, C32, C36, C37, C38, C56, C60, C61, C62, C80, C84, C85, C86, C104, C108, C109, C110, C128, C132, C133, C134: 0.1uF; 0402
C25, C39, C63, C87, C111, C135: 10uF; 0805
D1, D2, D3, D4, D5, D6: BLUE; LED-0603@1
E$1, E$2, E$3, E$4: FIDUCIAL-1X2
E$5, E$6: FIDUCIAL-1.5X3
F1, F2, F3, F4, F5, F6: 16V/2.5A(5A TRIP); 1812
FD1, FD2, FD3, FD4, FD5, FD6, FD7, FD8, FD9, FD10, FD11, FD12, FD13, FD14, FD15, FD16, FD17, FD18, FD19, FD20, FD21, FD22, FD23, FD24: FIDUCIALUFIDUCIAL; FIDUCIAL-MICRO
FRAME1, FRAME5, FRAME8, FRAME11, FRAME14, FRAME17: FRAME-LETTERNO_PACKAGE; DUMMY
FRAME2, FRAME3, FRAME4, FRAME6, FRAME7, FRAME9, FRAME10, FRAME12, FRAME13, FRAME15, FRAME16, FRAME18: FRAME-LEDGER; CREATIVE_COMMONS
H1, H2, H3, H4, H5, H6, H7, H8, H9, H10, H11, H12, H13, H14, H15, H16, H17, H18, H19, H20, H21, H22, H23, H24: STAND-OFFTIGHT; STAND-OFF-TIGHT
INT, INT1, INT2, INT3, INT4, INT5: SMT-JUMPER_2_NC_TRACE_SILK
J1, J19, J45, J67, J89, J111: JST04_1MM_RA
J2, J44, J66, J88, J110, J132: RASPBERRYPI-40-PIN-GPIO_SMD_STACKABLE_NOHOLES; RASPBERRY_PI_HAT_40_PIN_SMD_STACKABLE_NOHOLES
J3, J4, J5, J10, J35, J36, J37, J38, J57, J58, J59, J60, J79, J80, J81, J82, J101, J102, J103, J104, J123, J124, J125, J126: 1X03_LOCK
J6, J17, J21, J22, J32, J33, J41, J42, J54, J55, J63, J64, J76, J77, J85, J86, J98, J99, J107, J108, J120, J121, J129, J130: 1X01_NO_SILK
J7, J39, J61, J83, J105, J127: EXT SERVO PWR; 1X02
J8, J40, J62, J84, J106, J128: EXT 5V PWR; 1X02
J9, J13, J14, J16, J26, J28, J29, J31, J48, J50, J51, J53, J70, J72, J73, J75, J92, J94, J95, J97, J114, J116, J117, J119: 1X02_2.54_SCREWTERM_LG_DRILL
J11, J25, J47, J69, J91, J113: EXT MTR PWR; 1X02
J12, J15, J27, J30, J49, J52, J71, J74, J93, J96, J115, J118: 1X02_2.54_SCREWTERM
J18, J34, J56, J78, J100, J122: ISP; 2X3_TEST_POINTS
J20, J24, J46, J68, J90, J112: USB C; USB-C-16P
J23, J43, J65, J87, J109, J131: CORTEX_JTAG_DEBUG_PTH; 2X5-PTH-1.27MM
JP1, JP5, JP6, JP9, JP16, JP22, JP23, JP24, JP28, JP34, JP35, JP36, JP40, JP46, JP47, JP48, JP52, JP58, JP59, JP60, JP64, JP70, JP71, JP72: JUMPER-PAD-2; SMT-JUMPER_2_NC_TRACE_NO-SILK
JP2, JP7, JP25, JP37, JP49, JP61: FUSE BP; SMT-JUMPER_2_NO_SILK
JP3, JP8, JP26, JP38, JP50, JP62: I2C; SMT-JUMPER_3_2-NC_TRACE_SILK
JP4, JP14, JP27, JP39, JP51, JP63: PI ISO; SMT-JUMPER_2_NC_TRACE_SILK
JP10, JP11, JP12, JP17, JP18, JP19, JP29, JP30, JP31, JP41, JP42, JP43, JP53, JP54, JP55, JP65, JP66, JP67: JUMPER-PAD-2; SMT-JUMPER_2_NO_NO-SILK
JP13, JP15, JP20, JP21, JP32, JP33, JP44, JP45, JP56, JP57, JP68, JP69: ADR; SMT-JUMPER_2_NO_SILK
LOGO1, LOGO3, LOGO4, LOGO6, LOGO7, LOGO9, LOGO10, LOGO12, LOGO13, LOGO15, LOGO16, LOGO18: SFE_LOGO_NAME_FLAME.1_INCH; SFE_LOGO_NAME_FLAME_.1
LOGO2, LOGO5, LOGO8, LOGO11, LOGO14, LOGO17: OSHW-LOGOS; OSHW-LOGO-S
Q1, Q2, Q3, Q4, Q21, Q22, Q37, Q38, Q49, Q50, Q61, Q62: 310mA/60V/1.6Ω; SOT323
Q5, Q7, Q9, Q11, Q13, Q15, Q25, Q29, Q31, Q39, Q41, Q43, Q51, Q53, Q55, Q63, Q65, Q67: 20V/4.2A/52mΩ/1.4W; SOT23-3
Q6, Q8, Q10, Q12, Q14, Q16, Q26, Q30, Q32, Q40, Q42, Q44, Q52, Q54, Q56, Q64, Q66, Q68: SOT363_PHILIPS
Q17, Q18, Q19, Q20, Q23, Q24, Q27, Q28, Q33, Q34, Q35, Q36, Q45, Q46, Q47, Q48, Q57, Q58, Q59, Q60, Q69, Q70, Q71, Q72: 20V/0.2A/8MHz/1.2Ω/1Vth; SOT-416FL
R1, R2, R4, R5, R8, R13, R15, R17, R18, R19, R20, R21, R22, R23, R24, R31, R33, R34, R36, R37, R38, R39, R40, R41, R42, R43, R44, R60, R61, R62, R63, R64, R65, R66, R67, R68, R69, R74, R75, R76, R77, R78, R79, R80, R84, R86, R88, R98, R99, R100, R101, R102, R103, R104, R105, R106, R107, R112, R113, R114, R115, R116, R117, R118, R122, R124, R126, R136, R137, R138, R139, R140, R141, R142, R143, R144, R145, R150, R151, R152, R153, R154, R155, R156, R160, R162, R164, R174, R175, R176, R177, R178, R179, R180, R181, R182, R183, R188, R189, R190, R191, R192, R193, R194, R198, R200, R202, R212, R213, R214, R215, R216, R217, R218, R219, R220, R221, R226, R227, R228: 10k; 0603@1
R3, R6, R10, R11, R12, R28, R29, R70, R71, R72, R81, R82, R108, R109, R110, R119, R120, R146, R147, R148, R157, R158, R184, R185, R186, R195, R196, R222, R223, R224: 5.1k; 0603@1
R7, R9, R14, R30, R32, R35, R83, R85, R87, R121, R123, R125, R159, R161, R163, R197, R199, R201: 47k; 0603@1
R16, R45, R47, R50, R51, R52, R53, R54, R55, R56, R57, R58, R59, R73, R92, R93, R94, R95, R96, R97, R111, R130, R131, R132, R133, R134, R135, R149, R168, R169, R170, R171, R172, R173, R187, R206, R207, R208, R209, R210, R211, R225: 2.2k; 0402-TIGHT
R25, R26, R46, R48, R89, R90, R127, R128, R165, R166, R203, R204: 1; 0603@1
R27, R49, R91, R129, R167, R205: 470; 0603@1
TP0, TP1, TP2, TP3, TP6, TP7, TP8, TP10, TP11, TP12, TP13, TP14, TP15, TP16, TP17, TP18, TP20, TP21, TP22, TP23, TP26, TP27, TP28, TP30, TP31, TP32, TP33, TP34, TP35, TP36, TP37, TP38, TP40, TP41, TP42, TP43, TP46, TP47, TP48, TP50, TP51, TP52, TP53, TP54, TP55, TP56, TP57, TP58, TP60, TP61, TP62, TP63, TP66, TP67, TP68, TP70, TP71, TP72, TP73, TP74, TP75, TP76, TP77, TP78, TP80, TP81, TP82, TP83, TP86, TP87, TP88, TP90, TP91, TP92, TP93, TP94, TP95, TP96, TP97, TP98, TP100, TP101, TP102, TP103, TP106, TP107, TP108, TP110, TP111, TP112, TP113, TP114, TP115, TP116, TP117, TP118: PAD.03X.04
TP4, TP5, TP19, TP24, TP25, TP39, TP44, TP45, TP59, TP64, TP65, TP79, TP84, TP85, TP99, TP104, TP105, TP119: TP_15TH
TP9, TP29, TP49, TP69, TP89, TP109: TEST-POINT3X4; PAD.03X.04
U1, U2, U13, U19, U25, U31: PCA9685; TSSOP-28_4MM
U3, U5, U14, U20, U26, U32: DRV8835; WSON-12
U4, U12, U18, U24, U30, U36: ATTINY84-ARDUINO; SO14
U6, U9, U15, U21, U27, U33: CY8C4245LQI-483; QFN-40
U7, U10, U16, U22, U28, U34: 9DoF IMU; QFN24-3X3
U8, U11, U17, U23, U29, U35: 1.8V/100mA; SC70
U$1, U$28, U$191, U$286, U$381, U$476: QWIIC_LOGO_5MM; QWIIC_5MM
U$2, U$54, U$192, U$287, U$382, U$477: I_SUPER2_C-()-03
U$3, U$4, U$5, U$59, U$60, U$61, U$114, U$115, U$116, U$160, U$161, U$162, U$218, U$219, U$220, U$255, U$256, U$257, U$313, U$314, U$315, U$350, U$351, U$352, U$408, U$409, U$410, U$445, U$446, U$447, U$503, U$504, U$505, U$540, U$541, U$542: GND3
U$6, U$7, U$75, U$76, U$142, U$143, U$172, U$173, U$237, U$238, U$267, U$268, U$332, U$333, U$362, U$363, U$427, U$428, U$457, U$458, U$522, U$523, U$552, U$553: 10
U$8, U$79, U$146, U$176, U$241, U$271, U$336, U$366, U$431, U$461, U$526, U$556: 00
U$9, U$117, U$221, U$316, U$411, U$506: #MTR_RST5
U$10, U$118, U$222, U$317, U$412, U$507: #FSYNC7
U$11, U$119, U$223, U$318, U$413, U$508: #ENC_RST4
U$12, U$120, U$224, U$319, U$414, U$509: #ENC_INT6
U$13, U$52, U$121, U$155, U$225, U$250, U$320, U$345, U$415, U$440, U$510, U$535: EXT_PWR_INPUTS3
U$14, U$131, U$226, U$321, U$416, U$511: 5V2
U$15, U$132, U$227, U$322, U$417, U$512: MTR1
U$16, U$133, U$228, U$323, U$418, U$513: SERVO0
U$17, U$82, U$147, U$179, U$242, U$274, U$337, U$369, U$432, U$464, U$527, U$559: 11
U$18, U$19, U$182, U$183, U$277, U$278, U$372, U$373, U$467, U$468, U$562, U$563: 1X06_2.54_SCREWTERM_PIN_REF
U$20, U$21, U$65, U$66, U$134, U$135, U$164, U$165, U$229, U$230, U$259, U$260, U$324, U$325, U$354, U$355, U$419, U$420, U$449, U$450, U$514, U$515, U$544, U$545: B15
U$22, U$67, U$136, U$166, U$231, U$261, U$326, U$356, U$421, U$451, U$516, U$546: ENC112
U$23, U$68, U$137, U$167, U$232, U$262, U$327, U$357, U$422, U$452, U$517, U$547: ENC213
U$24, U$80, U$148, U$177, U$243, U$272, U$338, U$367, U$433, U$462, U$528, U$557: 22
U$25, U$81, U$149, U$178, U$244, U$273, U$339, U$368, U$434, U$463, U$529, U$558: 33
U$26, U$27, U$69, U$70, U$138, U$139, U$168, U$169, U$233, U$234, U$263, U$264, U$328, U$329, U$358, U$359, U$423, U$424, U$453, U$454, U$518, U$519, U$548, U$549: A14
U$29, U$64, U$195, U$290, U$385, U$480: STAT4
U$30, U$184, U$279, U$374, U$469, U$564: SRV_5#6V1
U$31, U$73, U$140, U$170, U$235, U$265, U$330, U$360, U$425, U$455, U$520, U$550: MTRA0
U$32, U$55, U$193, U$288, U$383, U$478: ISO1
U$33, U$41, U$71, U$186, U$196, U$281, U$291, U$376, U$386, U$471, U$481, U$566: 05
U$34, U$42, U$72, U$187, U$197, U$282, U$292, U$377, U$387, U$472, U$482, U$567: 16
U$35, U$63, U$194, U$289, U$384, U$479: PI0
U$36, U$45, U$84, U$188, U$198, U$283, U$293, U$378, U$388, U$473, U$483, U$568: 27
U$37, U$86, U$199, U$294, U$389, U$484: 38
U$38, U$185, U$280, U$375, U$470, U$565: MTR_5#9V0
U$39, U$153, U$248, U$343, U$438, U$533: IMU_ADR9
U$40, U$74, U$141, U$171, U$236, U$266, U$331, U$361, U$426, U$456, U$521, U$551: MTRB1
U$43, U$44, U$77, U$78, U$144, U$145, U$174, U$175, U$239, U$240, U$269, U$270, U$334, U$335, U$364, U$365, U$429, U$430, U$459, U$460, U$524, U$525, U$554, U$555: 21
U$46, U$189, U$284, U$379, U$474, U$569: MTR0
U$47, U$190, U$285, U$380, U$475, U$570: SRV_ADR0
U$48, U$150, U$245, U$340, U$435, U$530: ENC_INT12
U$49, U$151, U$246, U$341, U$436, U$531: ENC_ADR11
U$50, U$152, U$247, U$342, U$437, U$532: FUSE_BP10
U$51, U$154, U$249, U$344, U$439, U$534: MTR_ADR0
U$53, U$156, U$251, U$346, U$441, U$536: 5V3
U$56, U$157, U$252, U$347, U$442, U$537: #ENC_RST6
U$57, U$158, U$253, U$348, U$443, U$538: #MTR_RST7
U$58, U$159, U$254, U$349, U$444, U$539: #FSYNC8
U$62, U$163, U$258, U$353, U$448, U$543: #ENC_INT0
U$83, U$85, U$180, U$181, U$275, U$276, U$370, U$371, U$465, U$466, U$560, U$561: AUTOHAT-LOGO
U$87, U$93, U$97, U$100, U$103, U$109, U$123, U$126, U$200, U$206, U$210, U$213, U$295, U$301, U$305, U$308, U$390, U$396, U$400, U$403, U$485, U$491, U$495, U$498: X0
U$88, U$94, U$98, U$101, U$104, U$110, U$124, U$127, U$201, U$207, U$211, U$214, U$296, U$302, U$306, U$309, U$391, U$397, U$401, U$404, U$486, U$492, U$496, U$499: Y1
U$89, U$95, U$99, U$102, U$105, U$111, U$125, U$128, U$202, U$208, U$212, U$215, U$297, U$303, U$307, U$310, U$392, U$398, U$402, U$405, U$487, U$493, U$497, U$500: Z2
U$90, U$106, U$112, U$129, U$203, U$216, U$298, U$311, U$393, U$406, U$488, U$501: G5
U$91, U$107, U$113, U$130, U$204, U$217, U$299, U$312, U$394, U$407, U$489, U$502: A4
U$92, U$96, U$108, U$122, U$205, U$209, U$300, U$304, U$395, U$399, U$490, U$494: M3

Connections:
1.8V: C13.1, C14.1, Q23.1, Q24.1, Q27.1, Q28.1, R16.2, R45.2, R47.2, R53.2, R55.2, TP9.P$1, U7.8, U7.13, U7.22, U8.5
1.8V1: C41.1, C42.1, Q17.1, Q18.1, Q19.1, Q20.1, R50.2, R51.2, R52.2, R58.2, R73.2, TP29.P$1, U10.8, U10.13, U10.22, U11.5
1.8V2: C65.1, C66.1, Q33.1, Q34.1, Q35.1, Q36.1, R92.2, R93.2, R94.2, R96.2, R111.2, TP49.P$1, U16.8, U16.13, U16.22, U17.5
1.8V3: C89.1, C90.1, Q45.1, Q46.1, Q47.1, Q48.1, R130.2, R131.2, R132.2, R134.2, R149.2, TP69.P$1, U22.8, U22.13, U22.22, U23.5
1.8V4: C113.1, C114.1, Q57.1, Q58.1, Q59.1, Q60.1, R168.2, R169.2, R170.2, R172.2, R187.2, TP89.P$1, U28.8, U28.13, U28.22, U29.5
1.8V5: C137.1, C138.1, Q69.1, Q70.1, Q71.1, Q72.1, R206.2, R207.2, R208.2, R210.2, R225.2, TP109.P$1, U34.8, U34.13, U34.22, U35.5
3.3V: C2.1, C3.1, C7.1, C15.1, INT.2, J2.1, J2.1B, J2.17, J2.17B, J12.P2, J15.P1, J18.2, J19.2, J23.1, JP3.2, Q1.1, Q4.1, R3.2, R12.2, R22.2, R25.2, R26.2, R37.2, R39.2, R41.2, R43.1, R54.2, R56.2, TP19.P$1, U4.1, U5.12, U8.1, U8.3
3.3V1: C1.1, C28.1, C43.1, C44.1, INT1.2, J1.2, J27.P2, J30.P1, J34.2, J43.1, J44.1, J44.1B, J44.17, J44.17B, JP8.2, Q2.1, Q3.1, R46.2, R48.2, R57.2, R59.2, R60.2, R62.2, R64.2, R66.2, R68.1, R71.2, R72.2, TP39.P$1, U3.12, U11.1, U11.3, U12.1
3.3V2: C49.1, C52.1, C67.1, C68.1, INT2.2, J45.2, J49.P2, J52.P1, J56.2, J65.1, J66.1, J66.1B, J66.17, J66.17B, JP26.2, Q21.1, Q22.1, R89.2, R90.2, R95.2, R97.2, R98.2, R100.2, R102.2, R104.2, R106.1, R109.2, R110.2, TP59.P$1, U14.12, U17.1, U17.3, U18.1
3.3V3: C73.1, C76.1, C91.1, C92.1, INT3.2, J67.2, J71.P2, J74.P1, J78.2, J87.1, J88.1, J88.1B, J88.17, J88.17B, JP38.2, Q37.1, Q38.1, R127.2, R128.2, R133.2, R135.2, R136.2, R138.2, R140.2, R142.2, R144.1, R147.2, R148.2, TP79.P$1, U20.12, U23.1, U23.3, U24.1
3.3V4: C97.1, C100.1, C115.1, C116.1, INT4.2, J89.2, J93.P2, J96.P1, J100.2, J109.1, J110.1, J110.1B, J110.17, J110.17B, JP50.2, Q49.1, Q50.1, R165.2, R166.2, R171.2, R173.2, R174.2, R176.2, R178.2, R180.2, R182.1, R185.2, R186.2, TP99.P$1, U26.12, U29.1, U29.3, U30.1
3.3V5: C121.1, C124.1, C139.1, C140.1, INT5.2, J111.2, J115.P2, J118.P1, J122.2, J131.1, J132.1, J132.1B, J132.17, J132.17B, JP62.2, Q61.1, Q62.1, R203.2, R204.2, R209.2, R211.2, R212.2, R214.2, R216.2, R218.2, R220.1, R223.2, R224.2, TP119.P$1, U32.12, U35.1, U35.3, U36.1
5V: C8.1, F2.2, J8.2, JP2.2, Q5.3, Q6.1, Q7.3, Q8.1, Q9.3, Q10.1, R1.2, R2.2, R17.2, R18.2, R19.2, U1.28
5V1: C29.1, F1.2, J40.2, JP7.2, Q11.3, Q12.1, Q13.3, Q14.1, Q15.3, Q16.1, R20.2, R21.2, R74.2, R75.2, R76.2, U2.28
5V2: C53.1, F3.2, J62.2, JP25.2, Q25.3, Q26.1, Q29.3, Q30.1, Q31.3, Q32.1, R77.2, R78.2, R112.2, R113.2, R114.2, U13.28
5V3: C77.1, F4.2, J84.2, JP37.2, Q39.3, Q40.1, Q41.3, Q42.1, Q43.3, Q44.1, R115.2, R116.2, R150.2, R151.2, R152.2, U19.28
5V4: C101.1, F5.2, J106.2, JP49.2, Q51.3, Q52.1, Q53.3, Q54.1, Q55.3, Q56.1, R153.2, R154.2, R188.2, R189.2, R190.2, U25.28
5V5: C125.1, F6.2, J128.2, JP61.2, Q63.3, Q64.1, Q65.3, Q66.1, Q67.3, Q68.1, R191.2, R192.2, R226.2, R227.2, R228.2, U31.28
!ENC_INT: J2.7, J2.7B, J6.1, R33.1, U4.13
!ENC_INT1: J32.1, J44.7, J44.7B, R61.1, U12.13
!ENC_INT2: J54.1, J66.7, J66.7B, R99.1, U18.13
!ENC_INT3: J76.1, J88.7, J88.7B, R137.1, U24.13
!ENC_INT4: J98.1, J110.7, J110.7B, R175.1, U30.13
!ENC_INT5: J120.1, J132.7, J132.7B, R213.1, U36.13
!ENC_RST: J17.1, J18.5, R22.1, U4.4
!ENC_RST1: J33.1, J34.5, R60.1, U12.4
!ENC_RST2: J55.1, J56.5, R98.1, U18.4
!ENC_RST3: J77.1, J78.5, R136.1, U24.4
!ENC_RST4: J99.1, J100.5, R174.1, U30.4
!ENC_RST5: J121.1, J122.5, R212.1, U36.4
!FSYNC_1.8V: Q27.2, R53.1, U7.11
!FSYNC_1.8V1: Q19.2, R52.1, U10.11
!FSYNC_1.8V2: Q35.2, R94.1, U16.11
!FSYNC_1.8V3: Q47.2, R132.1, U22.11
!FSYNC_1.8V4: Q59.2, R170.1, U28.11
!FSYNC_1.8V5: Q71.2, R208.1, U34.11
!FSYNC_3.3V: J21.1, Q27.3, R54.1
!FSYNC_3.3V1: J41.1, Q19.3, R57.1
!FSYNC_3.3V2: J63.1, Q35.3, R95.1
!FSYNC_3.3V3: J85.1, Q47.3, R133.1
!FSYNC_3.3V4: J107.1, Q59.3, R171.1
!FSYNC_3.3V5: J129.1, Q71.3, R209.1
!MTR_RST: C23.1, J22.1, J23.10, U6.30
!MTR_RST1: C38.1, J42.1, J43.10, U9.30
!MTR_RST2: C62.1, J64.1, J65.10, U15.30
!MTR_RST3: C86.1, J86.1, J87.10, U21.30
!MTR_RST4: C110.1, J108.1, J109.10, U27.30
!MTR_RST5: C134.1, J130.1, J131.10, U33.30
AD0/SDO: JP15.2, R16.1, U7.9
AD0/SDO1: JP20.2, R73.1, U10.9
AD0/SDO2: JP32.2, R111.1, U16.9
AD0/SDO3: JP44.2, R149.1, U22.9
AD0/SDO4: JP56.2, R187.1, U28.9
AD0/SDO5: JP68.2, R225.1, U34.9
ADD_A0: JP1.2, R18.1, U1.1
ADD_A1: JP5.2, R17.1, U1.2
ADD_A2: JP6.2, R19.1, U1.3
ADD_A3: JP23.2, R74.1, U2.2
ADD_A4: JP22.2, R75.1, U2.1
ADD_A5: JP24.2, R76.1, U2.3
ADD_A6: JP35.2, R112.1, U13.2
ADD_A7: JP34.2, R113.1, U13.1
ADD_A8: JP36.2, R114.1, U13.3
ADD_A9: JP47.2, R150.1, U19.2
ADD_A10: JP46.2, R151.1, U19.1
ADD_A11: JP48.2, R152.1, U19.3
ADD_A12: JP59.2, R188.1, U25.2
ADD_A13: JP58.2, R189.1, U25.1
ADD_A14: JP60.2, R190.1, U25.3
ADD_A15: JP71.2, R226.1, U31.2
ADD_A16: JP70.2, R227.1, U31.1
ADD_A17: JP72.2, R228.1, U31.3
ADR: JP13.2, U4.3
ADR1: JP21.2, U12.3
ADR2: JP33.2, U18.3
ADR3: JP45.2, U24.3
ADR4: JP57.2, U30.3
ADR5: JP69.2, U36.3
AOUT1: J13.P1, TP16.P$1, U5.2
AOUT2: J13.P2, TP15.P$1, U5.3
AOUT3: J28.P1, TP36.P$1, U3.2
AOUT4: J28.P2, TP35.P$1, U3.3
AOUT5: J50.P1, TP56.P$1, U14.2
AOUT6: J50.P2, TP55.P$1, U14.3
AOUT7: J72.P1, TP76.P$1, U20.2
AOUT8: J72.P2, TP75.P$1, U20.3
AOUT9: J94.P1, TP96.P$1, U26.2
AOUT10: J94.P2, TP95.P$1, U26.3
AOUT11: J116.P1, TP116.P$1, U32.2
AOUT12: J116.P2, TP115.P$1, U32.3
BOUT1: J14.P1, TP14.P$1, U5.4
BOUT2: J14.P2, TP13.P$1, U5.5
BOUT3: J29.P1, TP34.P$1, U3.4
BOUT4: J29.P2, TP33.P$1, U3.5
BOUT5: J51.P1, TP54.P$1, U14.4
BOUT6: J51.P2, TP53.P$1, U14.5
BOUT7: J73.P1, TP74.P$1, U20.4
BOUT8: J73.P2, TP73.P$1, U20.5
BOUT9: J95.P1, TP94.P$1, U26.4
BOUT10: J95.P2, TP93.P$1, U26.5
BOUT11: J117.P1, TP114.P$1, U32.4
BOUT12: J117.P2, TP113.P$1, U32.5
CC1: J20.A5, R11.2
CC2: J20.B5, R10.2
CC3: J24.B5, R28.2
CC4: J24.A5, R29.2
CC5: J46.B5, R81.2
CC6: J46.A5, R82.2
CC7: J68.B5, R119.2
CC8: J68.A5, R120.2
CC9: J90.B5, R157.2
CC10: J90.A5, R158.2
CC11: J112.B5, R195.2
CC12: J112.A5, R196.2
CE0: J2.24, J2.24B
CE1: J44.24, J44.24B
CE2: J66.24, J66.24B
CE3: J88.24, J88.24B
CE4: J110.24, J110.24B
CE5: J132.24, J132.24B
CH0: J3.3, TP0.P$1, U1.6
CH1: J4.3, TP1.P$1, U1.7
CH2: J5.3, TP2.P$1, U1.8
CH3: J10.3, TP3.P$1, U1.9
CH4: J38.3, TP23.P$1, U2.9
CH5: J37.3, TP22.P$1, U2.8
CH6: J36.3, TP21.P$1, U2.7
CH7: J35.3, TP20.P$1, U2.6
CH8: J60.3, TP43.P$1, U13.9
CH9: J59.3, TP42.P$1, U13.8
CH10: J58.3, TP41.P$1, U13.7
CH11: J57.3, TP40.P$1, U13.6
CH12: J82.3, TP63.P$1, U19.9
CH13: J81.3, TP62.P$1, U19.8
CH14: J80.3, TP61.P$1, U19.7
CH15: J79.3, TP60.P$1, U19.6
CH16: J104.3, TP83.P$1, U25.9
CH17: J103.3, TP82.P$1, U25.8
CH18: J102.3, TP81.P$1, U25.7
CH19: J101.3, TP80.P$1, U25.6
CH20: J126.3, TP103.P$1, U31.9
CH21: J125.3, TP102.P$1, U31.8
CH22: J124.3, TP101.P$1, U31.7
CH23: J123.3, TP100.P$1, U31.6
CONFIG_OUT: R6.2, U6.10
CONFIG_OUT1: R70.2, U9.10
CONFIG_OUT2: R108.2, U15.10
CONFIG_OUT3: R146.2, U21.10
CONFIG_OUT4: R184.2, U27.10
CONFIG_OUT5: R222.2, U33.10
ENC1A_FILTERED: C16.1, R38.2, U4.2
ENC1A_FILTERED1: C46.1, R63.2, U12.2
ENC1A_FILTERED2: C70.1, R101.2, U18.2
ENC1A_FILTERED3: C94.1, R139.2, U24.2
ENC1A_FILTERED4: C118.1, R177.2, U30.2
ENC1A_FILTERED5: C142.1, R215.2, U36.2
ENC1A_RAW: J12.P1, R37.1, R38.1, TP17.P$1
ENC1A_RAW1: J27.P1, R62.1, R63.1, TP37.P$1
ENC1A_RAW2: J49.P1, R100.1, R101.1, TP57.P$1
ENC1A_RAW3: J71.P1, R138.1, R139.1, TP77.P$1
ENC1A_RAW4: J93.P1, R176.1, R177.1, TP97.P$1
ENC1A_RAW5: J115.P1, R214.1, R215.1, TP117.P$1
ENC1B_FILTERED: C11.1, R40.1, U4.11
ENC1B_FILTERED1: C45.1, R65.1, U12.11
ENC1B_FILTERED2: C69.1, R103.1, U18.11
ENC1B_FILTERED3: C93.1, R141.1, U24.11
ENC1B_FILTERED4: C117.1, R179.1, U30.11
ENC1B_FILTERED5: C141.1, R217.1, U36.11
ENC1B_RAW: J9.P2, R39.1, R40.2, TP18.P$1
ENC1B_RAW1: J26.P2, R64.1, R65.2, TP38.P$1
ENC1B_RAW2: J48.P2, R102.1, R103.2, TP58.P$1
ENC1B_RAW3: J70.P2, R140.1, R141.2, TP78.P$1
ENC1B_RAW4: J92.P2, R178.1, R179.2, TP98.P$1
ENC1B_RAW5: J114.P2, R216.1, R217.2, TP118.P$1
ENC2A_FILTERED: C27.1, R42.2, U4.6
ENC2A_FILTERED1: C48.1, R67.2, U12.6
ENC2A_FILTERED2: C72.1, R105.2, U18.6
ENC2A_FILTERED3: C96.1, R143.2, U24.6
ENC2A_FILTERED4: C120.1, R181.2, U30.6
ENC2A_FILTERED5: C144.1, R219.2, U36.6
ENC2A_RAW: J15.P2, R41.1, R42.1, TP12.P$1
ENC2A_RAW1: J30.P2, R66.1, R67.1, TP32.P$1
ENC2A_RAW2: J52.P2, R104.1, R105.1, TP52.P$1
ENC2A_RAW3: J74.P2, R142.1, R143.1, TP72.P$1
ENC2A_RAW4: J96.P2, R180.1, R181.1, TP92.P$1
ENC2A_RAW5: J118.P2, R218.1, R219.1, TP112.P$1
ENC2B_FILTERED: C26.1, R44.1, U4.5
ENC2B_FILTERED1: C47.1, R69.1, U12.5
ENC2B_FILTERED2: C71.1, R107.1, U18.5
ENC2B_FILTERED3: C95.1, R145.1, U24.5
ENC2B_FILTERED4: C119.1, R183.1, U30.5
ENC2B_FILTERED5: C143.1, R221.1, U36.5
ENC2B_RAW: J16.P1, R43.2, R44.2, TP11.P$1
ENC2B_RAW1: J31.P1, R68.2, R69.2, TP31.P$1
ENC2B_RAW2: J53.P1, R106.2, R107.2, TP51.P$1
ENC2B_RAW3: J75.P1, R144.2, R145.2, TP71.P$1
ENC2B_RAW4: J97.P1, R182.2, R183.2, TP91.P$1
ENC2B_RAW5: J119.P1, R220.2, R221.2, TP111.P$1
GND: C2.2, C3.2, C5.-, C6.2, C7.2, C8.2, C10.2, C11.2, C12.2, C13.2, C14.2, C15.2, C16.2, C17.2, C18.2, C19.2, C20.2, C21.2, C22.2, C23.2, C24.2, C25.2, C26.2, C27.2, D2.C, J2.6, J2.6B, J2.9, J2.9B, J2.14, J2.14B, J2.20, J2.20B, J2.25, J2.25B, J2.30, J2.30B, J2.34, J2.34B, J2.39, J2.39B, J3.1, J4.1, J5.1, J7.1, J8.1, J9.P1, J10.1, J11.1, J16.P2, J18.6, J19.1, J20.GND, J20.GND2, J23.3, J23.5, J23.7, J23.9, JP1.1, JP5.1, JP6.1, JP9.1, JP10.1, JP11.1, JP12.1, JP13.1, JP15.1, R6.1, R7.1, R8.1, R9.1, R10.1, R11.1, R13.1, R14.1, R15.1, U1.4, U1.5, U1.14, U1.23, U1.25, U4.14, U5.6, U5.PAD, U6.9, U6.34, U6.EP, U7.18, U7.20, U8.2
GND1: C1.2, C4.-, C9.2, C28.2, C29.2, C30.2, C31.2, C32.2, C33.2, C34.2, C35.2, C36.2, C37.2, C38.2, C39.2, C40.2, C41.2, C42.2, C43.2, C44.2, C45.2, C46.2, C47.2, C48.2, D1.C, J1.1, J24.GND, J24.GND2, J25.1, J26.P1, J31.P2, J34.6, J35.1, J36.1, J37.1, J38.1, J39.1, J40.1, J43.3, J43.5, J43.7, J43.9, J44.6, J44.6B, J44.9, J44.9B, J44.14, J44.14B, J44.20, J44.20B, J44.25, J44.25B, J44.30, J44.30B, J44.34, J44.34B, J44.39, J44.39B, JP16.1, JP17.1, JP18.1, JP19.1, JP20.1, JP21.1, JP22.1, JP23.1, JP24.1, R28.1, R29.1, R30.1, R31.1, R32.1, R34.1, R35.1, R36.1, R70.1, U2.4, U2.5, U2.14, U2.23, U2.25, U3.6, U3.PAD, U9.9, U9.34, U9.EP, U10.18, U10.20, U11.2, U12.14
GND2: C49.2, C50.-, C51.2, C52.2, C53.2, C54.2, C55.2, C56.2, C57.2, C58.2, C59.2, C60.2, C61.2, C62.2, C63.2, C64.2, C65.2, C66.2, C67.2, C68.2, C69.2, C70.2, C71.2, C72.2, D3.C, J45.1, J46.GND, J46.GND2, J47.1, J48.P1, J53.P2, J56.6, J57.1, J58.1, J59.1, J60.1, J61.1, J62.1, J65.3, J65.5, J65.7, J65.9, J66.6, J66.6B, J66.9, J66.9B, J66.14, J66.14B, J66.20, J66.20B, J66.25, J66.25B, J66.30, J66.30B, J66.34, J66.34B, J66.39, J66.39B, JP28.1, JP29.1, JP30.1, JP31.1, JP32.1, JP33.1, JP34.1, JP35.1, JP36.1, R81.1, R82.1, R83.1, R84.1, R85.1, R86.1, R87.1, R88.1, R108.1, U13.4, U13.5, U13.14, U13.23, U13.25, U14.6, U14.PAD, U15.9, U15.34, U15.EP, U16.18, U16.20, U17.2, U18.14
GND3: C73.2, C74.-, C75.2, C76.2, C77.2, C78.2, C79.2, C80.2, C81.2, C82.2, C83.2, C84.2, C85.2, C86.2, C87.2, C88.2, C89.2, C90.2, C91.2, C92.2, C93.2, C94.2, C95.2, C96.2, D4.C, J67.1, J68.GND, J68.GND2, J69.1, J70.P1, J75.P2, J78.6, J79.1, J80.1, J81.1, J82.1, J83.1, J84.1, J87.3, J87.5, J87.7, J87.9, J88.6, J88.6B, J88.9, J88.9B, J88.14, J88.14B, J88.20, J88.20B, J88.25, J88.25B, J88.30, J88.30B, J88.34, J88.34B, J88.39, J88.39B, JP40.1, JP41.1, JP42.1, JP43.1, JP44.1, JP45.1, JP46.1, JP47.1, JP48.1, R119.1, R120.1, R121.1, R122.1, R123.1, R124.1, R125.1, R126.1, R146.1, U19.4, U19.5, U19.14, U19.23, U19.25, U20.6, U20.PAD, U21.9, U21.34, U21.EP, U22.18, U22.20, U23.2, U24.14
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

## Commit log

2020-02-05 Finalized power input options, schematic almost done, routing started
    [SparkFun_Robo_HAT.brd, SparkFun_Robo_HAT.sch]
2020-02-06 Most labeling done, pwr and motor lines routed
    [SparkFun_Robo_HAT.brd, SparkFun_Robo_HAT.sch]
2020-02-07 Routing done, waiting on logo from marcom
    [SparkFun_Robo_HAT.brd, SparkFun_Robo_HAT.sch]
2020-02-07 version number in bottom copper
    [SparkFun_Robo_HAT.brd]
2020-02-10 vector fonts in schematic
    [SparkFun_Robo_HAT.sch]
2020-02-10 sch cleanup and drc stuff in brd
    [SparkFun_Robo_HAT.brd, SparkFun_Robo_HAT.sch]
2020-02-10 removed USB C Shield polygon
    to let more GND flow under connector up to Pi Header.
    [SparkFun_Robo_HAT.brd, SparkFun_Robo_HAT.sch]
2020-02-10 added product name to top silk
    [SparkFun_Robo_HAT.brd]
2020-02-10 flipped I2C label to match others, added name to bsilk, aligned other labels
    [SparkFun_Robo_HAT.brd]
2020-02-10 added fuse bits to read me
2020-02-10 Engineer 1st run of checklist
    added measures and SS path, cleaned up sch a bit more.
    [SparkFun_Robo_HAT.brd, SparkFun_Robo_HAT.sch]
2020-02-10 post design review changes
    -moved TP P3.0 programming pSoc onto grid
    -Added pulldown resistor on Config line on PSoc
    -Added trestric under pSoC to avoid GND pad nubbins.
    -Added pullup resistors to SDA_OUT and SCL_OUT, as consistent with original serial controlled motor driver.
    -Switched over to design block for pi header and slots. re-routed some stuff to make it work.
    [SparkFun_Robo_HAT.brd, SparkFun_Robo_HAT.sch]
2020-02-10 moved to non-altered fab limit DRC and fix GND pour to extend to top
    [SparkFun_Robo_HAT.brd]
2020-02-12 post double-check changes - ready for proto v01
    -moved TP6 to SMT pad style and on grid
    -updated tran-14386 (ideal diode) to have polarity mark outside package
    -nudged vias to avoid silk labels
    [SparkFun_Robo_HAT.brd, SparkFun_Robo_HAT.sch]
2020-02-12 proto gerbers v01
    [SparkFun_Robo_HAT.GBL, SparkFun_Robo_HAT.GBO, SparkFun_Robo_HAT.GBP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]
2020-02-21 Connected IMU CS pin to 1.8V, Added IMU ADR PU 2.2K resistor
    [SparkFun_Robo_HAT.brd, SparkFun_Robo_HAT.sch]
2020-02-21 bumped version to v10 in sch and brd
    [SparkFun_Robo_HAT.brd, SparkFun_Robo_HAT.sch]
2020-02-21 moving to SMD stackable solution... 99 done
    [SparkFun_Robo_HAT.brd, SparkFun_Robo_HAT.sch]
2020-02-24 Added LOGO, improved GND pour flowing
    -added LOGO to top and bottom silk
    -rerouted some traces on right side of board near the EXT headers to allow for better GND flow
    -added more gnd vias near SMD pads on stackable header package
    -removed pesky test point values in SCH
    [SparkFun_Robo_HAT.brd, SparkFun_Robo_HAT.sch]
2020-02-24 Design review changes
    -added more GND stiching VIAs to middle area of board (MTR VIN trace kind of cutts top GND pour in half diagnoly)
    -rotated IMU axis labels to read same as other silk
    -separated imu axis labels on bottom silk
    -removed GND traces from Cypress thermal pad to GND pads
    -added more gnd vias under cypress
    -removed TP15 name text in SCH
    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
    [SparkFun_Robo_HAT.brd, SparkFun_Robo_HAT.sch]
2020-02-24 update single unit gerbers
    [SparkFun_Robo_HAT.GBL, SparkFun_Robo_HAT.GBO, SparkFun_Robo_HAT.GBP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]
2020-02-24 dimension line width to 0.008 inch
    [SparkFun_Robo_HAT.brd]
2020-02-24 added test point to 3.3V rail
    [SparkFun_Robo_HAT.brd, SparkFun_Robo_HAT.sch]
2020-02-24 Cleaned up and fixed dimensions
    [SparkFun_Robo_HAT.brd]
2020-02-25 production panel and gerbers v10
    [SparkFun_Robo_HAT-Panel.GBL, SparkFun_Robo_HAT-Panel.GBO, SparkFun_Robo_HAT-Panel.GBP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]
2020-02-25 fixed vector font issue on servo "~"
    -bumped version to v11
    -also updated the "+" and "-" symbols on servo headers and encoder terminals (on both top silk and bottom silk) I drew everything with wires so they look clean and will hold position through the panelizer ulp tool
    [SparkFun_Robo_HAT.brd, SparkFun_Robo_HAT.sch]
2020-02-25 removing unneeded single unit gerbers and other unneeded files
    [SparkFun_Robo_HAT-Panel.GBL, SparkFun_Robo_HAT-Panel.GBO, SparkFun_Robo_HAT-Panel.GBP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]
2020-02-25 renaming files to correct product name
    no other changes made, just name of files
    [SparkFun_Auto_pHAT.brd, SparkFun_Auto_pHAT.sch]
2020-02-25 TP19 (3.3V) moved to bottom, to expose bStop
    [SparkFun_Auto_pHAT.brd]
2020-02-25 panelized v11, renamed zip file for production
    [SparkFun_Auto_pHAT-Panel.GBL, SparkFun_Auto_pHAT-Panel.GBO, SparkFun_Auto_pHAT-Panel.GBP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]
2020-02-25 Added missing vertical vscore on panel
    [SparkFun_Auto_pHAT-Panel.brd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]
2020-03-18 v12
    -moved stat LED to side for easier rework and better visibility
    -added holes to let air through to SHIM Fan (when it sits flush up to the PCB, there is no room for airflow)
    -bumped version to v12 in copper and all 3 sheets in sch
    [SparkFun_Auto_pHAT.brd, SparkFun_Auto_pHAT.sch]
2020-03-18 Adjusted screwpin terminal fp and locations to work with 1x2s and 1x6s
    [SparkFun_Auto_pHAT.brd, SparkFun_Auto_pHAT.sch]
2020-03-19 Design Review changes
    -Decreased 5V trace by Pi 40pin 5V header pad, to avoid tStop overlap.
    -Decreased SDA and SCL trace width to 0.007 inch near pi header (in the uppder left of board) to avoid bStop overlap on those traces.
    -Added Voltage ranges to pin labels on EXT power inputs (bottom silk labels only)
    [SparkFun_Auto_pHAT.brd]
2020-03-20 Added Address jumpers for Servo IC
    -Added 3 address jumpers to Servo IC. (includes a BOM change to include 3 more 10K resistors) This will allow for up to 8 different addresses. Note, A4 and A5 are permenantly connected to GND.
    -Added address table to SCH for address jumpers.
    -increased one of the "fan" holes to allow for even more airflow using the SHIM fan.
    [SparkFun_Auto_pHAT.brd, SparkFun_Auto_pHAT.sch]
2020-03-20 Changed SVR ADD label to SVR ADR (to match others)
    [SparkFun_Auto_pHAT.brd]
2020-03-22 Checklist run #1 on v12
    -prod ids on smt 2x20
    [SparkFun_Auto_pHAT.brd, SparkFun_Auto_pHAT.sch]
2020-03-23 v12 gerbers
    [SparkFun_Auto_pHAT-Panel.GBL, SparkFun_Auto_pHAT-Panel.GBO, SparkFun_Auto_pHAT-Panel.GBS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]

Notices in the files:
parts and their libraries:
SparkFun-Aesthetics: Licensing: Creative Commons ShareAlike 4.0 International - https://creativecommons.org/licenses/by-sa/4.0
